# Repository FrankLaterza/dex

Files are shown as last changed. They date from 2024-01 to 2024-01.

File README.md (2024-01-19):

# Dex
An open source self balancing robot designed for the Raspberry Pi Pico and controlled by a DS4 controller. Dex was made with 3D printed ABS, a custom PCB, and a whole lot of patience. This repository shall serve as a reference for anyone making their own balancing robot. The code is well formatted for your convenience you nerd. Note this is an intermediate project so take your time and have fun.

<div style="display:flex; justify-content:center;">
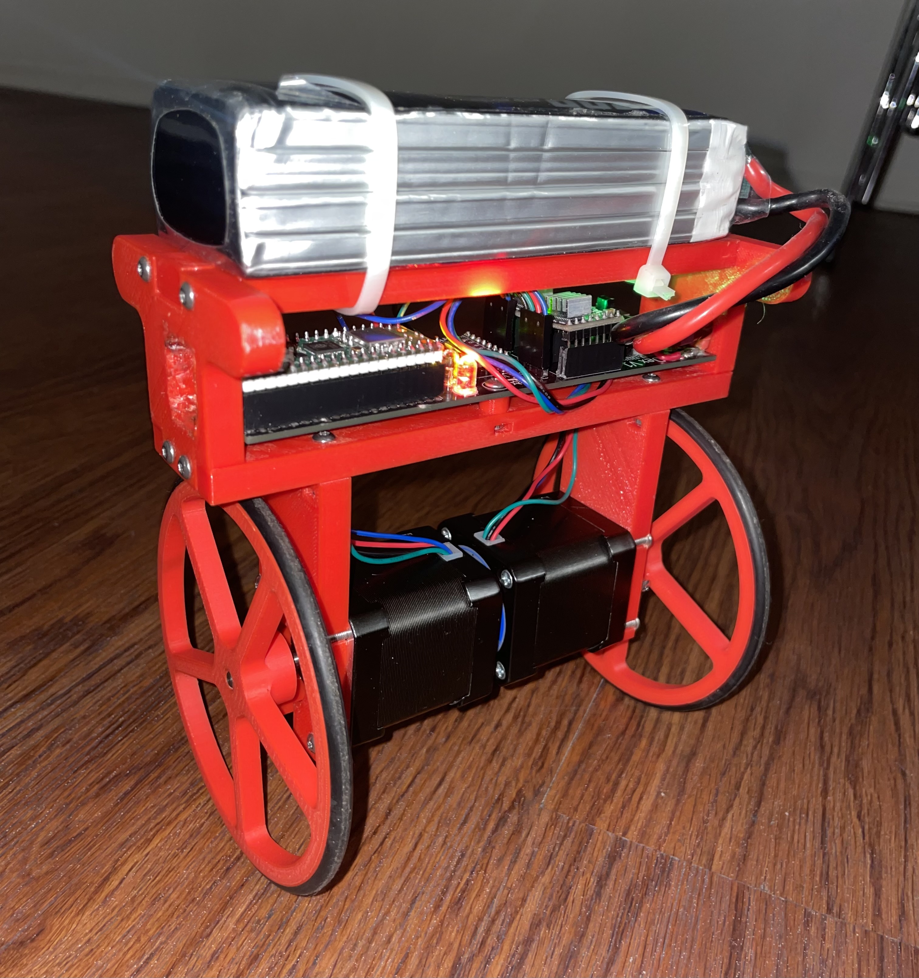
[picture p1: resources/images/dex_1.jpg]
  
</div>
<br/>

## Software
This project uses the several libraries including FreeRTOS, BTstack, and the Pico SDK. Each is a specific versions and can be setup with a recursive git clone. For this project the software utilizes both cores on the RP2040.
_
### Core 0
The primary purpose of core 0 is to handle all of the CWY43 SPI and MPU6050 I2C interrupts that hog all the cpu.

### Core 1
The FreeRTOS scheduler runs on this core to prevent conflicting timing with the SPI interrupted. The bluetooth callback also gets processed here. 

| FreeRTOS Scheduler Tasks | Description | Task Delay us |
| ----- | ---- | ---- |
| stat_led_task | blinky blinky | 500000us |
| bt_hid_inputs | process controller inputs | 20000us |
| stepper_left_task | controls the left stepper | varying per step |
| stepper_right_task | controls the right stepper | varying per step  |
| mpu6050_task | requests gyro/accelerometer data and processed roll angle with Kalman filter | 20000us |
| pid_task | calculates the output for the stepper motors | 10000us |
| good_boy_task | watches the dog | 500000us |

### Overclocking
Please note this project overclock the RP2040 to 250MHz and configures the configTICK_RATE_HZ 100000 (10us period). This is to give enough time for the schedule overhead. The reason for the high tick rate is because the steppers need step at very high rates.

## PCB 
This PCB was made in Eagle Cad and can find the PCB under resources/pcb. Please note there are two mistakes that i've hand wired for this current pcb. The holes for the switch are too small and cut traces to make the switch come before the 5V regulator. I'll update the files with a fixed design soon.

<div style="display:flex; justify-content:center;">
  
</div>

## CAD
This project was designed in Fusion 360 and all the files can be found under resources/cad. 
<div style="display:flex; justify-content:center;">
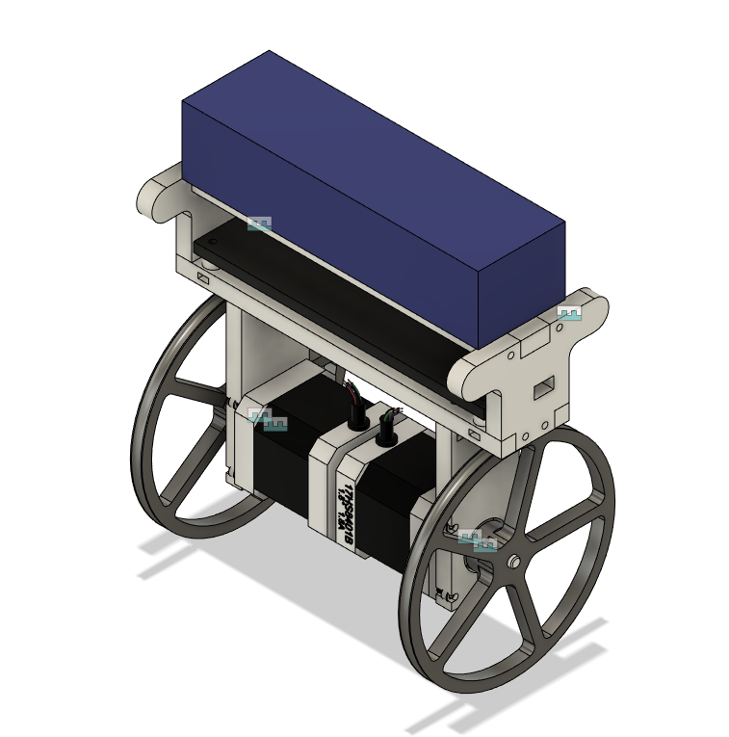
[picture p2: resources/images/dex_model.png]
  
</div>

## BOM 💣

| Name | Count | Price (meets count) | Description | Rating | Notes | Link |
|---|---|---|---|---|---|---|
| Raspberry Pi PIco W | 1 | $18.96 | MPU | Clock: 135MHz | 2 Cores | [Amazon Link](https://www.amazon.com/gp/product/B0B72GV3K3/ref=ewc_pr_img_12?smid=A1PI3LRUETBKN8&psc=1) |
| PCB | 1 | $24.05 | Custom PCB designed | Engineering Level: Maximum | Designed in Eagle and order on JLCPCB | N/A |
| NEMA 17 Stepper | 2 | $13.99 | Main Motors | Max Current 2a | | [Amazon Link](https://www.amazon.com/gp/product/B0B72GV3K3/ref=ewc_pr_img_12?smid=A1PI3LRUETBKN8&psc=1) |
| Stepper Driver A4988 | 2 | $14.99 | Drives the stepper motors | Min Step Rate: 500kHz | | [Amazon Link](https://www.amazon.com/gp/product/B09X382335/ref=ewc_pr_img_2?smid=A1VTL661FOEJB1&th=1) |
| MPU-6050 | 1 | $7.59 | 3 Axis Gryo and Accelerometer | 16bit | | [Amazon Link](https://www.amazon.com/gp/product/B0B3D6D1KD/ref=ppx_yo_dt_b_search_asin_title?ie=UTF8&psc=1) |
| L7805CV | 1 | $8.59 | 5V Voltage Regulator | 35Vin and 5Vout/1.5A | | [Amazon Link](https://www.amazon.com/gp/product/B0CBKCDT4H/ref=ewc_pr_img_1?smid=A3FX7C4A9P37IQ&th=1) |
| Power Switch | 1 | $6.99 | AC 125V 2A | | Only cuts power 5V power not stepper input voltage | [Amazon Link](https://www.amazon.com/gp/product/B099N61GTZ/ref=ewc_pr_img_3?smid=A3KX1QBS9AS0L7&th=1) |
| LED | 4 | $11.99 | | Forward Voltage: R/Y 2.0-2.2V; B/G/W 3.0-3.2V; Max. Current: 20mA | User about 100Ohm resistor | [Amazon Link](https://www.amazon.com/DiCUNO-450pcs-Colors-Emitting-Assorted/dp/B073QMYKDM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) |
| Beeper | 1 | $7.99 | Active beeeper | 2.5-4V/25mA. | Make sure to be extra annoying | [Amazon Link](https://www.amazon.com/gp/product/B07VRK7ZPF/ref=ewc_pr_img_5?smid=A10PG8DP5LW0Q1&psc=1) |
| Resistors | 4 | $5.99 | Resistor for LEDS | | | [Amazon Link](https://www.amazon.com/MCIGICM-Values-Resistor-Assortment-Resistors/dp/B06WRQS97C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) |
| Headers | N/A | $7.99 | Used for PCB and IO | | | [Amazon Link](https://www.amazon.com/2-54mm-Breakaway-Female-Connector-Arduino/dp/B01MQ48T2V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) |
| Battery | 1 | $44.99 | Any 4s Lipo will work | 4S Lipo Battery 5200mAh 14.8V 60C | | [Amazon Link](https://www.amazon.com/Pairs-Connector-Female-Silicon-Battery/dp/B07QM1WS2J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) |
| O rings | 2 | $5.99 | Goes over 3d printed wheel for grip | 110mm OD 100mm ID 5mm Width | I used the wheels from Wouter [here](https://elexperiment.nl/2018/11/high-speed-balancing-robot-introduction/) | [Amazon Link](https://www.amazon.com/gp/product/B07GXFKGNT/ref=ppx_yo_dt_b_search_asin_title?ie=UTF8&th=1) |
| 3D Printed Chassis | 1 | 0 | Main body of the robot | | Designed in Fusion 360 | N/A |
| 3D printed Wheels | 2 | 0 | Main wheels with rubber O rings | Designed in Fusion 360 CREDIT DESIGN | | N/A |

## Known Issues
* Sometimes the program will halt when trying to connect to the BT HID.
* Cannot reconnect to pico after pair to another controller.

## Starting Debugger
Plug in debugger and run:
```
openocd -f interface/cmsis-dap.cfg -c "adapter speed 5000" -f target/rp2040.cfg -s tcl
```
confrim this starts on localhost:3333

open another terminal and run:
```
gdb-multiarch dex.elf
```
in this termincal type the command
```
target remote localhost:3333
```
load with 
```
load
```

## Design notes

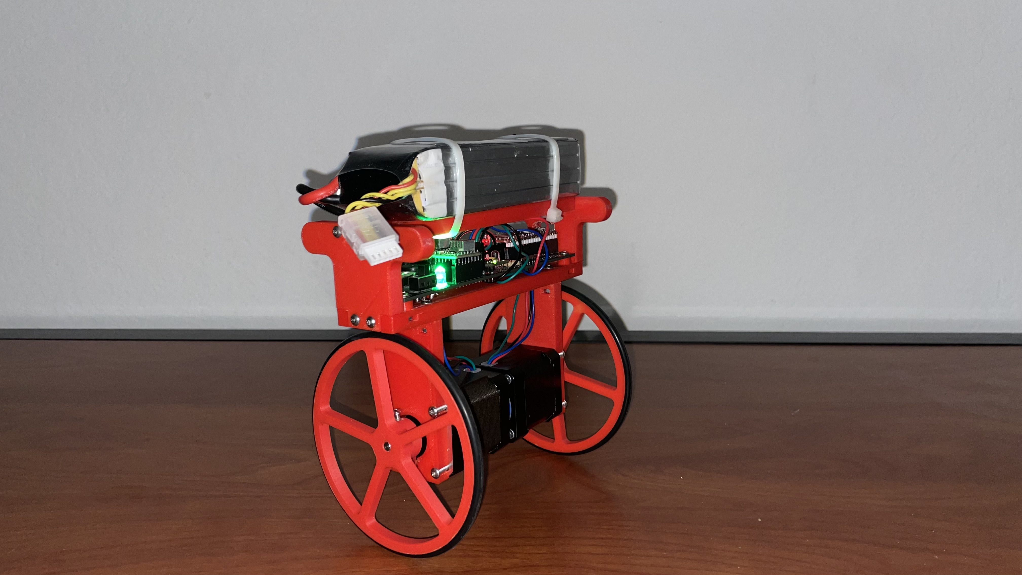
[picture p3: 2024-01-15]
resources/images/dex_2.jpg

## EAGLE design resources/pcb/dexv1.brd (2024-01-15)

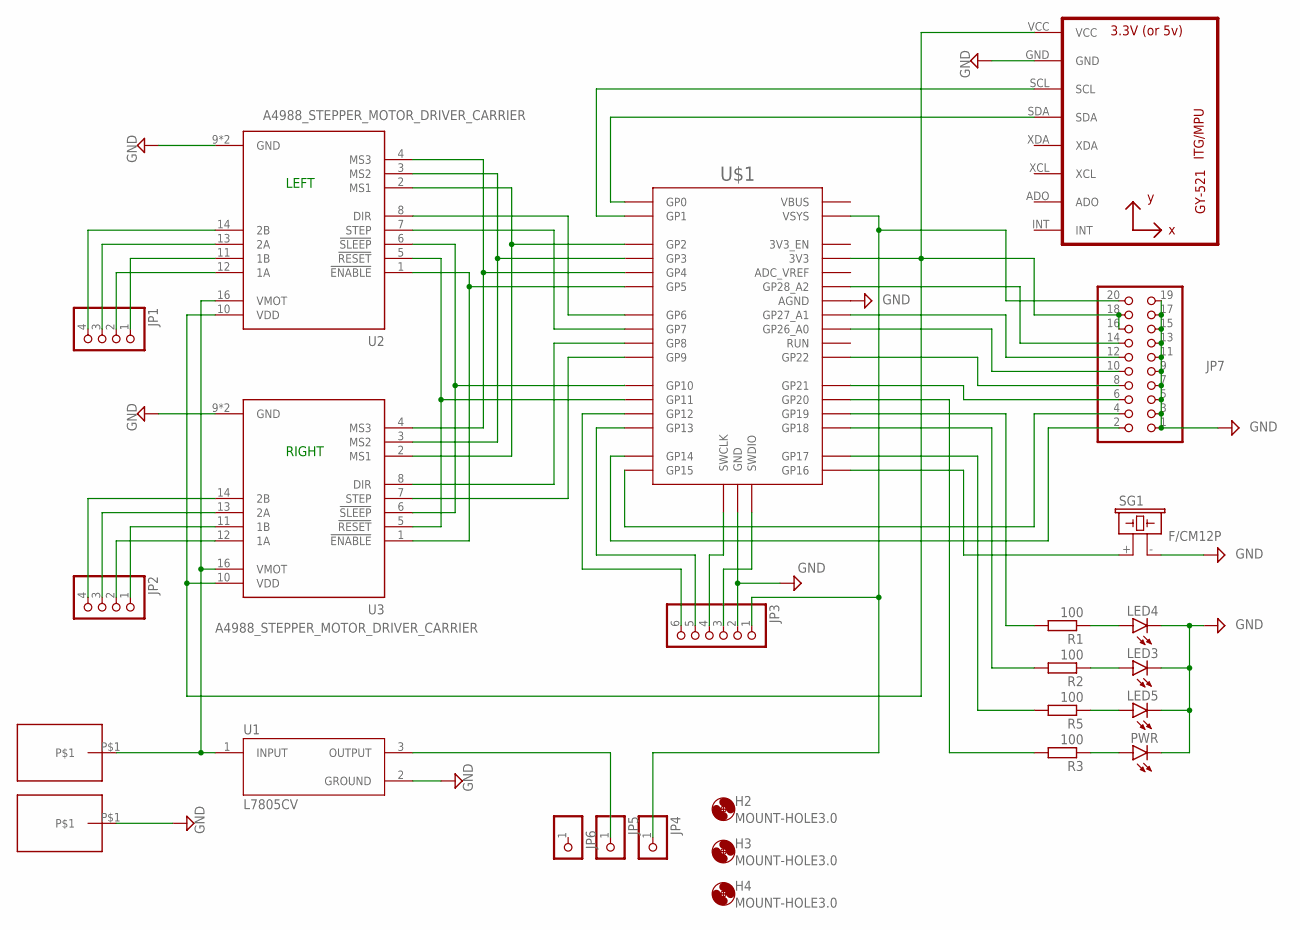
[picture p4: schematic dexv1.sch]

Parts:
H2, H3, H4: MOUNT-HOLE3.0; 3,0
JP1, JP2: PINHD-1X4; 1X04
JP3: PINHD-1X6; 1X06
JP4, JP5, JP6: PINHD-1X1; 1X01
JP7: PINHD-2X10; 2X10
LED3, LED4, LED5: LED5MM
PWR: LED5MM
R1, R2, R3, R5: 100; 0204/7
SG1: F/CM12P
U1: L7805CV; TO255P1040X460X1968-3
U2, U3: A4988_STEPPER_MOTOR_DRIVER_CARRIER; MODULE_A4988_STEPPER_MOTOR_DRIVER_CARRIER
U4: GY-521MPU6050; GY-521
U$1: RPI_PICO-TH; RPI_PICO_TH
U$2, U$3: SMD5X10

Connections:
GND: JP3.2, JP7.1, JP7.3, JP7.5, JP7.7, JP7.9, JP7.11, JP7.13, JP7.15, JP7.17, JP7.19, LED3.K (C), LED4.K (C), LED5.K (C), PWR.K (C), SG1.- (2), U1.2 (GROUND), U2.9 (GND), U2.15 (GND), U3.9 (GND), U3.15 (GND), U4.GND, U$1.AGND, U$1.GND@1 (GND), U$1.GND@2 (GND), U$1.GND@3 (GND), U$1.GND@4 (GND), U$1.GND@5 (GND), U$1.GND@6 (GND), U$1.GND@7 (GND), U$1.GND@8 (GND), U$1.P$2 (GND), U$3.P$1
unnamed: JP2.2, U3.12 (1A)
unnamed: U4.SDA, U$1.GP0
unnamed: JP7.14, U$1.GP28_A2
unnamed: U2.4 (MS3), U3.4 (MS3), U$1.GP4
unnamed: U2.3 (MS2), U3.3 (MS2), U$1.GP3
unnamed: U2.2 (MS1), U3.2 (MS1), U$1.GP2
unnamed: U2.8 (DIR), U$1.GP6
unnamed: U2.7 (STEP), U$1.GP7
unnamed: U3.8 (DIR), U$1.GP8
unnamed: U2.1 (!ENABLE), U3.1 (!ENABLE), U$1.GP5
unnamed: U3.7 (STEP), U$1.GP9
unnamed: U2.6 (!SLEEP), U3.6 (!SLEEP), U$1.GP10
unnamed: U2.5 (!RESET), U3.5 (!RESET), U$1.GP11
unnamed: JP1.2, U2.12 (1A)
unnamed: JP1.1, U2.11 (1B)
unnamed: JP1.3, U2.13 (2A)
unnamed: JP1.4, U2.14 (2B)
unnamed: JP2.1, U3.11 (1B)
unnamed: JP2.3, U3.13 (2A)
unnamed: JP2.4, U3.14 (2B)
unnamed: JP3.1, JP4.1, JP7.20, U$1.VSYS
unnamed: JP5.1, U1.3 (OUTPUT)
unnamed: JP7.4, U$1.GP15
unnamed: SG1.+ (1), U$1.GP16
unnamed: U4.SCL, U$1.GP1
unnamed: LED4.A, R1.1
unnamed: LED3.A, R2.1
unnamed: R5.2, U$1.GP17
unnamed: LED5.A, R5.1
unnamed: JP3.6, U$1.GP12
unnamed: JP3.3, U$1.P$3 (SWDIO), U$1.SWDIO
unnamed: JP3.4, U$1.P$1 (SWCLK), U$1.SWCLK
unnamed: JP3.5, U$1.GP13
unnamed: JP7.10, U$1.GP26_A0
unnamed: R1.2, U$1.GP19
unnamed: R2.2, U$1.GP18
unnamed: JP7.12, U$1.GP27_A1
unnamed: JP7.8, U$1.GP22
unnamed: JP7.6, U$1.GP21
unnamed: U1.1 (INPUT), U2.16 (VMOT), U3.16 (VMOT), U$2.P$1
unnamed: JP7.16, JP7.18, U2.10 (VDD), U3.10 (VDD), U4.VCC, U$1.3V3
unnamed: JP7.2, U$1.GP14
unnamed: PWR.A, R3.1
unnamed: R3.2, U$1.GP20

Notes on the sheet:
LEFT
RIGHT

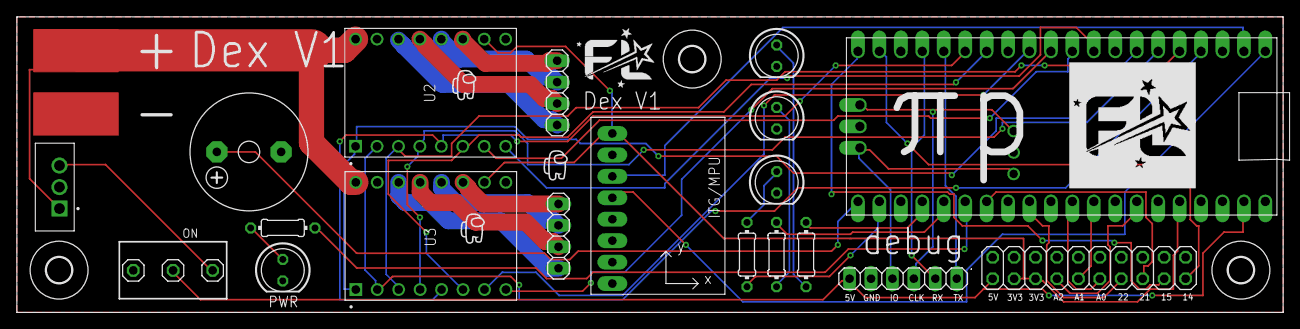
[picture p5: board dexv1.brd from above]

Board: 2 copper layers, 150.0 x 35.0 mm, 26 parts (0 on the bottom side), 45 nets.

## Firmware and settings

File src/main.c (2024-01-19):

#include "FreeRTOS.h"
#include "bt_hid.h"
#include "btstack.h"
#include "classic/sdp_server.h"
#include "controls.h"
#include "hardware/flash.h"
#include "hardware/timer.h"
#include "hardware/watchdog.h"
#include "mpu6050.h"
#include "pico/async_context.h"
#include "pico/cyw43_arch.h"
#include "pico/flash.h"
#include "pico/multicore.h"
#include "pico/stdlib.h"
#include "pid.h"
#include "pinout.h"
#include "semphr.h"
#include "stepper.h"
#include "task.h"
#include "utils.h"
#include <stdint.h>
#include <stdio.h>
#include <string.h>

#define CORE_0 (1 << 0)
#define CORE_1 (1 << 1)

// all GLOBALS (see utils)
SemaphoreHandle_t g_mutex_print;
bool g_bt_packet_gaurd = false;
char g_print_buf[1024];
uint32_t g_step_delay_period_us_left = 3000;
uint32_t g_step_delay_period_us_right = 3000;
float g_current_angle_roll;
float g_current_angle_pitch;
bool is_bt_connected = false;
float g_target_rpm = 0;
float g_steer = 0;
float g_step_count_left = 0;
float g_step_count_right = 0;

void bt_hid_inputs(void *pvParameters) {
    wait_for_bt_connect();
    struct bt_hid_state controls;
    while (true) {
        g_bt_packet_gaurd = true;
        controls = bt_hid_get_latest_lazy();
        g_bt_packet_gaurd = false;
        process_hid_controls(controls);
        vTaskDelay(US_TO_RTOS_TICK(20000));
    }
}

void stat_led_task(void *pvParameters) {
    wait_for_bt_connect();
    int interval = US_TO_RTOS_TICK(500000);
    while (true) {
        gpio_put(STAT_LED_1, LOW);
        gpio_put(STAT_LED_2, HIGH);
        vTaskDelay(interval);
        gpio_put(STAT_LED_2, LOW);
        gpio_put(STAT_LED_1, HIGH);
        vTaskDelay(interval);
    }
}

void mpu6050_task(void *pvParameters) {
    wait_for_bt_connect();
    while (true) {
        mpu6050_poll();
        vTaskDelay(US_TO_RTOS_TICK(20000));
    }
}

struct stopwatch_t stopwatch;
static int64_t elapsed_time_total;

void stepper_left_task(void *pvParameters) {
    wait_for_bt_connect();
    while (true) {
        // stopwatch.start_time = get_absolute_time();
        // add steps
        g_step_count_left += (direction_moving(LEFT) ? -1.0 : 1.0) / get_stepper_step_size(LEFT);
        set_stepper_step_size(LEFT);
        gpio_put(STEP_L, HIGH);
        vTaskDelay(US_TO_RTOS_TICK(g_step_delay_period_us_left));
        // stopwatch.end_time = get_absolute_time();
        // elapsed_time_total = absolute_time_diff_us(stopwatch.start_time, stopwatch.end_time);
        // sprintf(g_print_buf, "step delay: %dus, elapsed time: %lldus\n", g_step_delay_period_us_left, elapsed_time_total);
        // vGuardedPrint(g_print_buf);
        set_stepper_step_size(LEFT);
        gpio_put(STEP_L, LOW);
        vTaskDelay(US_TO_RTOS_TICK(g_step_delay_period_us_left));
    }
}

void stepper_right_task(void *pvParameters) {
    wait_for_bt_connect();
    while (true) {
        g_step_count_right += (direction_moving(RIGHT) ? 1.0 : -1.0) / get_stepper_step_size(RIGHT);
        set_stepper_step_size(RIGHT);
        gpio_put(STEP_R, HIGH);
        vTaskDelay(US_TO_RTOS_TICK(g_step_delay_period_us_right));

        set_stepper_step_size(RIGHT);
        gpio_put(STEP_R, LOW);
        vTaskDelay(US_TO_RTOS_TICK(g_step_delay_period_us_right));
    }
}

void pid_task(void *pvParameters) {
    wait_for_bt_connect();
    pid_init_balance();
    while (true) {
        balance();
        vTaskDelay(US_TO_RTOS_TICK(10000));
    }
}

void good_boy_task() {
    // pet the dog 🐕
    while (true) {
        watchdog_update();
        vTaskDelay(US_TO_RTOS_TICK(500000));
    }
}

void start_core1() {
    bt_hid_init();
    vTaskStartScheduler();
    bt_main(); // does not return
}

int main() {
    // run the setup script
    pinout_init();
    // create a mutex
    g_mutex_print = xSemaphoreCreateMutex();

    TaskHandle_t stat_led;
    TaskHandle_t inputs;
    TaskHandle_t stepper_left;
    TaskHandle_t stepper_right;
    TaskHandle_t mpu6050;
    TaskHandle_t pid;
    TaskHandle_t good_boy;

    // TODO check task timing and align accordingly
    xTaskCreate(stat_led_task, "stat_led", 256, NULL, 5, &stat_led);
    xTaskCreate(bt_hid_inputs, "inputs", 256, NULL, 3, &inputs);
    xTaskCreate(stepper_left_task, "stepper_left", 256, NULL, 1, &stepper_left);
    xTaskCreate(stepper_right_task, "stepper_right", 256, NULL, 1, &stepper_right);
    xTaskCreate(mpu6050_task, "mpu6050", 256, NULL, 2, &mpu6050);
    xTaskCreate(pid_task, "pid", 256, NULL, 2, &pid);
    xTaskCreate(good_boy_task, "good_boy", 256, NULL, 6, &good_boy);

    // beep after setup
    beep(3, 50);

    // TODO check resources. what core is i2c running on?
    flash_safe_execute_core_init();
    multicore_launch_core1(start_core1);

    while (true) {
        /* do nothing */
    }

    return 1;
}

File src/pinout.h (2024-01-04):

#ifndef PINOUT_H
#define PINOUT_H

#define STAT_LED_0 18 // bt led
#define STAT_LED_1 19 // stat 1
#define STAT_LED_2 17 // stat 2
#define PWR_LED 20
#define BUZZER 16 // BUZZZZZZZ
#define STEP_L 7
#define STEP_R 9
#define DIR_L 6
#define DIR_R 8 
#define MS1 2
#define MS2 3
#define MS3 4
#define ENABLE 5
#define SLEEP 10
#define RESET 11
#define I2C_SDA 0
#define I2C_SCL 1
#define I2C_INST i2c0
#define HIGH 1
#define LOW 0

void pinout_init();


#endif

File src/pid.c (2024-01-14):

#include "pid.h"
#include "kalman.h"
#include "math.h"
#include "pico/stdlib.h"
#include "stepper.h"
#include "utils.h"
#include <stdbool.h>
#include <stdio.h>

#define MAX_TARGET_ANGLE_ABSOLUTE 40
#define MAX_POSITION_ANGLE_ABSOLUTE 10
#define POSITION_LOCK_THRESHOLD_ABSOLUTE 10

static struct pid_t pid_wheels;
static struct pid_t pid_rpm;
static struct pid_t pid_position;
/*
 * the average of the left and right rpm is taken
 * because we want to know the velocity vector
 * related to the center fo the robot. regardless
 * during turning the offset of rpm will be applied
 * to both left and right the same.
 */
static float center_balance = -4.5;
static float angle_offset = 0;
static float rpm_balance = 0;
static float average_rpm = 0;
static float rpm_left = 0;
static float rpm_right = 0;
static float step_count_avg = 0;
float steer_map = 0;
static bool position_lock = true;

void pid_init(struct pid_t *pid, float kp, float ki, float kd, float max_windup) {
    pid->kp = kp;
    pid->ki = ki;
    pid->kd = kd;
    pid->p = 0;
    pid->i = 0;
    pid->d = 0;
    pid->error = 0;
    pid->error_last = 0;
    pid->max_windup = max_windup;
}

float pid_calc(struct pid_t *pid, float current, float target) {
    // record the last p
    pid->error_last = pid->error;
    // update the error
    pid->error = target - current;
    // direct feedback
    pid->p = pid->kp * pid->error;
    // integrate with windup
    pid->i = convert_from_range_float(pid->i + pid->error, -pid->max_windup, pid->max_windup);
    // derive
    pid->d = pid->kd * (pid->error - pid->error_last);
    // the magic
    return pid->p + (pid->ki * pid->i) + pid->d;
}

void pid_init_balance() {
    // TODO tune
    pid_init(&pid_wheels, 1.7, 0.001, 11, 200);
    pid_init(&pid_rpm, 0.03, 0.001, 0.045, 2000);
    pid_init(&pid_position, 0.001, 0.003, 0.3, 400);
}

// main balancing script
void balance() {
    if (fabs(g_current_angle_roll) >= 60) {
        disable_stepper();
        return;
    }
    // accelerate to target rpm
    if (fabs(g_target_rpm) > 1) {
        // get target angle
        angle_offset = pid_calc(&pid_rpm, average_rpm, g_target_rpm);
        position_lock = false; // we are moving
        angle_offset = convert_from_absolute_range_float(angle_offset, MAX_TARGET_ANGLE_ABSOLUTE);
    }
    // lock onto position
    else if (position_lock) {
        step_count_avg = (g_step_count_left + g_step_count_right) / 2;
        angle_offset = pid_calc(&pid_position, step_count_avg, 0);
        angle_offset = convert_from_absolute_range_float(angle_offset, MAX_POSITION_ANGLE_ABSOLUTE);
    }
    // there is no target and we aren't fast so enable pos lock
    else if (fabs(average_rpm) < POSITION_LOCK_THRESHOLD_ABSOLUTE) {
        // toggle position lock after its been set false by target rpm
        position_lock = true;
        g_step_count_left = 0;
        g_step_count_right = 0;
    }
    // decelerate
    else {
        angle_offset = pid_calc(&pid_rpm, average_rpm, 0);
        angle_offset = convert_from_absolute_range_float(angle_offset, MAX_TARGET_ANGLE_ABSOLUTE);
    }

    // angle_offset = convert_from_absolute_range_float(angle_offset, MAX_OFFSET_ANGLE_ABSOLUTE);
    rpm_balance = pid_calc(&pid_wheels, g_current_angle_roll, center_balance - angle_offset);
    average_rpm += rpm_balance / 2;
    average_rpm = convert_from_absolute_range_float(average_rpm, MAX_RPM_ABSOLUTE);

    // map the steer based on how fast we are going
    steer_map = g_steer * (1 - (average_rpm / (MAX_RPM_ABSOLUTE + 20)));

    // drive left and right motors
    drive_motors_rpm(average_rpm + steer_map, average_rpm - steer_map);
}

void print_balance_stats() {
    sprintf(g_print_buf, "target rpm: %f, average rpm: %f, angle offset: %f, current angle: %f, steps l/r: %f/%f ",
            g_target_rpm, average_rpm, angle_offset, g_current_angle_roll, step_count_avg, steer_map);
    vGuardedPrint(g_print_buf);
}

void tune_center_up() {
    center_balance += 0.05;
}

void tune_center_down() {
    center_balance -= 0.05;
}

void reset_balance() {
    average_rpm = 0;
    rpm_left = 0;
    rpm_right = 0;
    g_step_count_left = 0;
    g_step_count_right = 0;
    angle_offset = 0;
    rpm_balance = 0;
    step_count_avg = 0;
    position_lock = true;
}

void do_nothing() {
    return;
};

void print_star() {
    sprintf(g_print_buf, "*");
    vGuardedPrint(g_print_buf);
}

void print_tweaker(uint8_t tune_select) {
    // print by a page
    if (tune_select <= 3) {
        vGuardedPrint("| pid wheels: ");
        tune_select == 0 ? print_star() : do_nothing();
        sprintf(g_print_buf, "w-kp: %f, ", pid_wheels.kp);
        vGuardedPrint(g_print_buf);
        tune_select == 1 ? print_star() : do_nothing();
        sprintf(g_print_buf, "w-ki: %f, ", pid_wheels.ki);
        vGuardedPrint(g_print_buf);
        tune_select == 2 ? print_star() : do_nothing();
        sprintf(g_print_buf, "w-kd: %f, ", pid_wheels.kd);
        vGuardedPrint(g_print_buf);
        tune_select == 3 ? print_star() : do_nothing();
        sprintf(g_print_buf, "w-mw: %f | ", pid_wheels.max_windup);
        vGuardedPrint(g_print_buf);
    } else if (tune_select <= 7) {
        vGuardedPrint("| pid rpm: ");
        tune_select == 4 ? print_star() : do_nothing();
        sprintf(g_print_buf, "r-kp: %f, ", pid_rpm.kp);
        vGuardedPrint(g_print_buf);
        tune_select == 5 ? print_star() : do_nothing();
        sprintf(g_print_buf, "r-ki: %f, ", pid_rpm.ki);
        vGuardedPrint(g_print_buf);
        tune_select == 6 ? print_star() : do_nothing();
        sprintf(g_print_buf, "r-kd: %f, ", pid_rpm.kd);
        vGuardedPrint(g_print_buf);
        tune_select == 7 ? print_star() : do_nothing();
        sprintf(g_print_buf, "r-mw: %f | ", pid_rpm.max_windup);
        vGuardedPrint(g_print_buf);
    } else {
        vGuardedPrint("| pid position: ");
        tune_select == 8 ? print_star() : do_nothing();
        sprintf(g_print_buf, "p-kp: %f, ", pid_position.kp);
        vGuardedPrint(g_print_buf);
        tune_select == 9 ? print_star() : do_nothing();
        sprintf(g_print_buf, "p-ki: %f, ", pid_position.ki);
        vGuardedPrint(g_print_buf);
        tune_select == 10 ? print_star() : do_nothing();
        sprintf(g_print_buf, "p-kd: %f, ", pid_position.kd);
        vGuardedPrint(g_print_buf);
        tune_select == 11 ? print_star() : do_nothing();
        sprintf(g_print_buf, "p-mw: %f | ", pid_position.max_windup);
        vGuardedPrint(g_print_buf);
    }
}
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

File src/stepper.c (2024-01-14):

#include "stepper.h"
#include "pico/stdlib.h"
#include "pid.h"
#include "pinout.h"
#include "utils.h"
#include <math.h>
#include <stdint.h>
#include <stdio.h>

// static vars only live here
static uint8_t step_size_l = FULL;
static uint8_t step_size_r = FULL;
static bool dir_left = false;
static bool dir_right = false;

void enable_stepper() {
    // enable the motor
    gpio_put(SLEEP, HIGH);
    gpio_put(RESET, HIGH);
    reset_balance();
}

void disable_stepper() {
    // disable the motor
    gpio_put(SLEEP, LOW);
    gpio_put(RESET, LOW);
}

void set_direction(bool stepper, bool direction) {
    // left stepper
    if (stepper) {
        gpio_put(DIR_L, direction);
        dir_left = direction;
    }
    // right stepper
    else {
        gpio_put(DIR_R, direction);
        dir_right = direction;
    }
}

// returns true if forward false if backward for a given stepper
bool direction_moving(bool stepper) {
    return stepper ? dir_left : dir_right;
}

uint8_t rpm_step_profile(float rpm) {
    uint8_t step_size;

    // if (rpm > MIN_RPM_FULL) {
    //     step_size = FULL;
    // }
    if (rpm > MIN_RPM_HALF) {
        step_size = HALF;
    } else if (rpm > MIN_RPM_FOURTH) {
        step_size = FOURTH;
    } else {
        step_size = EIGHTH;
    }
    // } else {
    //     step_size = SIXTEENTH;
    // }
    return step_size;
}

/*
 * converts rpm into steps per micro second
 * note this will be the perfect instantaneous delay
 */
uint32_t rpm_to_step_delay_us(bool stepper, float rpm) {
    uint8_t step_size = stepper ? step_size_l : step_size_r;

    if (rpm == 0) {
        return MAX_STEP_TASK_DELAY;
    }
    // revolutions per second
    float rps = rpm / 60;
    // degrees per second
    float dps = rps * 360;
    // steps per second
    float sps = dps / (STEP_ANGLE / step_size);
    // step delay period (div by 2 because delay twice)
    float delay_period_s = (1 / sps) / 2;
    // get the us delay
    int32_t delay_period_us = delay_period_s * 1000000;
    // return the goods
    return min((uint32_t)delay_period_us, MAX_STEP_TASK_DELAY);
}

uint32_t rpm_to_step_delay_us_fast(bool stepper, float rpm) {
    uint8_t step_size = stepper ? step_size_l : step_size_r;
    if (rpm == 0) {
        return MAX_STEP_TASK_DELAY;
    }
    float delay_period_us = ((RPM_US_CONVERSION_MAGIC * STEP_ANGLE) / (rpm * step_size));
    int32_t round = delay_period_us;
    return min((uint32_t)round, MAX_STEP_TASK_DELAY);
}

// drives both stepper motor based on an rpm
void drive_motors_rpm(float rpm_l, float rpm_r) {
    // drive the left and right motor in the appropriate direction
    rpm_l > 0 ? set_direction(LEFT, BACKWARD) : set_direction(LEFT, FORWARD);
    rpm_r > 0 ? set_direction(RIGHT, FORWARD) : set_direction(RIGHT, BACKWARD);

    rpm_l = convert_from_absolute_range_float(rpm_l, MAX_RPM_ABSOLUTE);
    rpm_r = convert_from_absolute_range_float(rpm_r, MAX_RPM_ABSOLUTE);

    // store the step size (only changes in stepper task)
    step_size_l = rpm_step_profile(fabs(rpm_l));
    step_size_r = rpm_step_profile(fabs(rpm_r));

    // get the step delay
    uint32_t step_delay_l = rpm_to_step_delay_us_fast(LEFT, fabs(rpm_l));
    uint32_t step_delay_r = rpm_to_step_delay_us_fast(RIGHT, fabs(rpm_r));

    // sprintf(g_print_buf, "l rpm: %f, l step size: %u, l step delay: %u\n", rpm_l, step_size_l, step_delay_r);
    // vGuardedPrint(g_print_buf);

    // drive motor
    g_step_delay_period_us_left = step_delay_l;
    g_step_delay_period_us_right = step_delay_r;
}

void set_step_size(uint8_t step_config) {
    if (step_config == FULL) {
        gpio_put(MS1, LOW);
        gpio_put(MS2, LOW);
        gpio_put(MS3, LOW);
    } else if (step_config == HALF) {
        gpio_put(MS1, HIGH);
        gpio_put(MS2, LOW);
        gpio_put(MS3, LOW);
    } else if (step_config == FOURTH) {
        gpio_put(MS1, LOW);
        gpio_put(MS2, HIGH);
        gpio_put(MS3, LOW);
    } else if (step_config == EIGHTH) {
        gpio_put(MS1, HIGH);
        gpio_put(MS2, HIGH);
        gpio_put(MS3, LOW);
    } else if (step_config == SIXTEENTH) {
        gpio_put(MS1, HIGH);
        gpio_put(MS2, HIGH);
        gpio_put(MS3, HIGH);
    }
}

void set_stepper_step_size(uint8_t stepper) {
    set_step_size(stepper ? step_size_l : step_size_r);
}

uint8_t get_stepper_step_size(uint8_t stepper) {
    return stepper ? step_size_l : step_size_r;
}

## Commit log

2023-12-22 pico-sdk hash
2023-12-31 stepper wip
